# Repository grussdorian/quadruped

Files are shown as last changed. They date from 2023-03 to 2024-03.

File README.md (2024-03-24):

# Final presentation video
[Part 1](https://youtu.be/GLVumrYQS3o)
[Part 2](https://youtu.be/F0bNzEO_wMU)

# Final Paper link

[A Framework for Seamless Trajectory Estimation and Navigation of Robotic Sensor Platform with Resource-Constrained Embedded Controller](https://ieeexplore.ieee.org/abstract/document/10324982)

# Documentation for Pupper

1. [Parts sourcing](#1-parts-sourcing)
2. [Assembly](#2-assembly)
3. [Connections](#3-connections)
4. [Code](#4-code)
5. [Calibration](#5-calibration)
6. [Running the robot](#6-running-the-robot)
7. [Controlling](#7-controlling)
8. [Things which are still left](#8-things-to-do)
9. [Checklist of things before connecting the PCB to the RPi](#9-checklist-of-things-which-are-needed-before-connecting-the-pcb-to-the-raspberry-pi)

## 1. Parts sourcing.

Please refer to [This spreadsheet](https://docs.google.com/spreadsheets/d/1AzzCM8UDrbhDfgtIsiQplI5SMlo7OLG8/edit#gid=1202520655). Part sourcing is listed here comprehensively.

For building the quadruped's body and legs, we have used 5mm fibre sheets. Ideally it should be carbon fibre. But we could not find a vendor who could cut the carbon fibre sheets according to our specifications. Also laser cutting of carbon fibre is not possible in the lab. The next best choice was to use acrylic fibre and that is what we used. $3$ mm thickness for legs and $5$ mm thickness for the base and top.

All the structural elements are taken from [here](https://a360.co/2TEh4gQ)
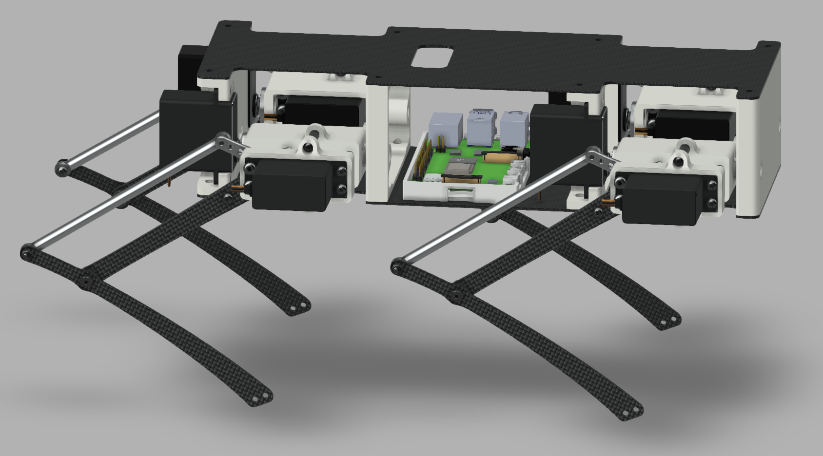
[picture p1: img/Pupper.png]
Pupper Codey the Codecademy mascot (https://stanford195.autodesk360.com/g/shares/SH919a0QTf3c32634dcfedf61e031f673710)


### Laser Cut parts

| Part name | Quantity | Thickness (mm) |
| --- | --- | --- |
| Acrylic fibre plate top | 1 | 5 |
| Acrylic fibre plate bottm | 1 | 5 |
| Lower leg | 4 | 3 |
| Upper leg | 4 | 3 |

To obtain the design of the above parts, we extracted each of the above mentioned prefab from the fusion 360 model. For laser cutting, we had to project the legs, and the base on a 2d surface in fusion, and extract the traces. Then we used laser cad for some final retouching.

_Note:_ The design provided here has two holes in the upper legs, both of them are useless as they do not fit our servo horn. So we had to modify the position of the hole in laser CAD to be $0.85$ mm from the beginning of the curvature. **[Update]** We have used mild steel to make the legs, as the acrylic legs could not handle the heavy weight of the robot

**[Update]** The design of the upper leg has been modified and now we are not using the plastic disc to prevent slipping. Instead we have prototyped (with acrylic) a leg with two holes which fit perfectly in the two holes of the leg. [We are going to laser cut it in aluminum.](#8-things-to-do)

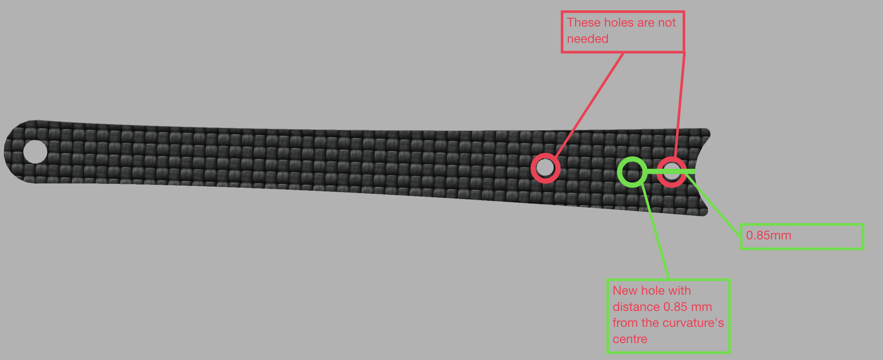
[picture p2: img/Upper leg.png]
Upper Leg


**[Update]** The design of the upper leg has once again been modified. This time there is no disc attached to the upper leg. Instead the concave shape of the upper leg has been changed to a convex shape, with two M3 screw holes. Thus the need for adding a disc has been eliminated.

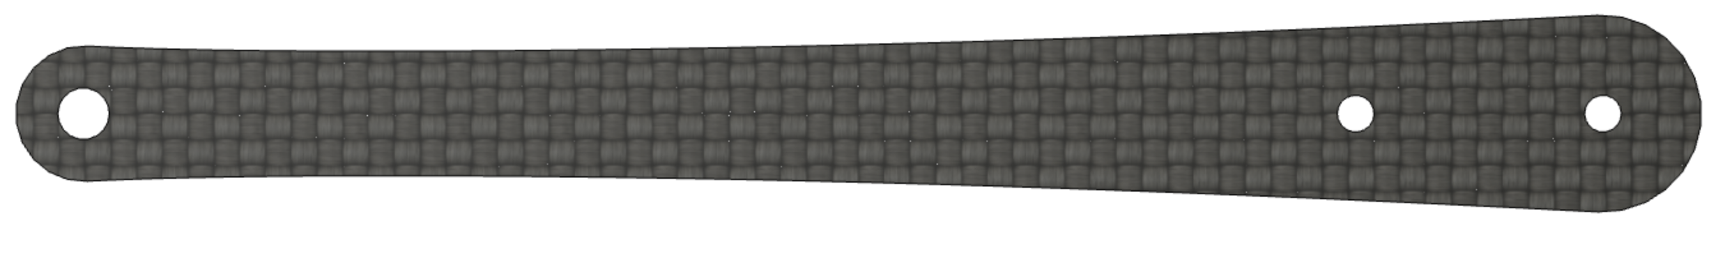
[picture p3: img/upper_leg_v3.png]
Upper Leg


### 3D printed parts

_Note that the 3D printed parts had holes much bigger than the size of the inserts. So the inserts did not fit in the holes. Instead we tried to use nuts and washers to tighten the screws where the inserts would have gone_

For the 3D printed Structures, we used PLA or PETG, 0.2mm-0.4mm layer height, >50% infill.

| Part name | STL name | Quantity |
| --- | --- | --- |
| Body support - "Front1" | FrontFront.stl | 1 |
| Body support - "Front2" | FrontBack.stl | 1 |
| Body support - "Back1"  | BackFront.stl | 1 |
| Body support - "Back2"  | BackBack.stl | 1 |
| Inner Hip | HipInsideFDM.stl  | 4 |
| Outer Hip | HipOutsideFDM.stl | 4 |

All the parts are uploaded in the [3D printed files](/3DPrintedFiles/)

After all the raw materials and parts are available, we can move to assembly

### PCB

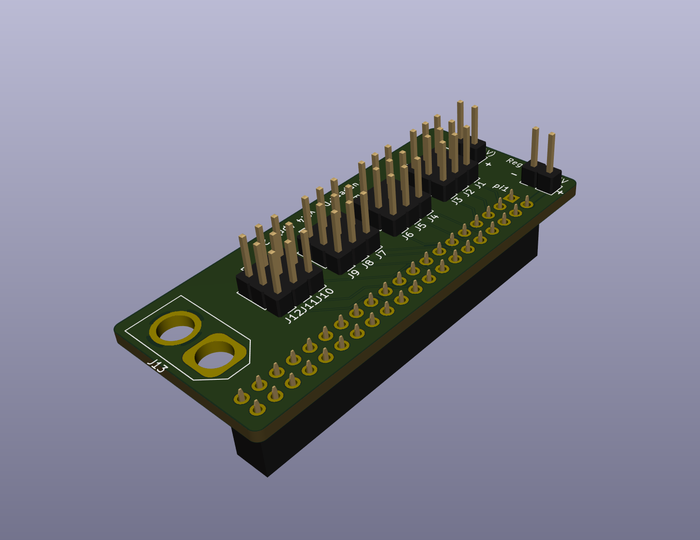
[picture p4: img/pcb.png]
PCB
 required to power all the servos, provide signal from the Raspberry Pi. It sits on top of the GPIO pins of the Pi. It can also be used to power the Pi [something we messed up doing](#what-went-wrong).
The [Gerber files](https://github.com/stanfordroboticsclub/Pupper-Raspi-PDB/) could be used to print the PCB using any standard PCB manufacturer. _NOTE_ 2 oz copper should be used for the traces. After getting the PCB, we need to solder the headers as shown in the image. Solder a pigtail connector wire in J13 to connect the battery. Make sure that the pigtail wire is joined above (side facing the male headers) the PCB. Solder the female $20\times2$ female header on the back side of the PCB.

**[Update]** There was jittering, (i.e incorrect pwm signals) in for J3. So we had to cut out the header for the signal pin of J3 and attach a jumper wire from GPIO pin `20` to signal socket of J3 directly. In future PCBs This change is to be [incorporated](#8-things-to-do)

## 2. Assembly

Pupper has 4 legs, each with 3 sets of [servos](https://robokits.co.in/motors/rc-servo-motor/ultra-torque-metal-gear-35kgcm-coreless-stainless-steel-pinion-standard-servo-motor). These servos are placed inside 3D printed hip joints.

### All reference images are placed under folder [img](/img)

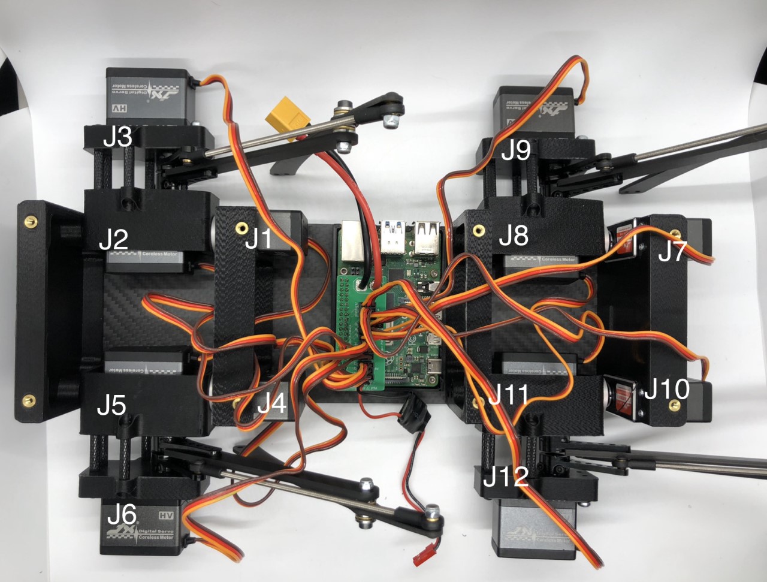
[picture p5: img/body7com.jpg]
Servo placement and numbering


### Hip assembly

All the servos should be housed inside hip joints in the following way:

1. First, screw metallic disc with $J1,J4,J7,J10$. _Important_: apply some hot glue after fixing the disc tightly with the servo.

2. Take inner hip and screw 4 black m4x6 screws that came with the servos to the disc.

3. Place $J2,J5,J8,J11$ in the inner hip and use m3x20 screws to tighten the side of the hip facing away from the disc.

4. _Note:_ Tightening should be enough such that the screw pokes out from the other side of the inner hip. Here we need to fasten the 20mm spacers. Tighten the servo with m3x10 screws (for the remaining two holes)

_Choice of the screw is important. The horn should be facing away from the 4 spacers and should be able to rotate freely without any obstruction. So the screws should be tightened upto that extent only which does not cause any obstruction in the horn's way_

5. Place the other set of 20mm spacers on the screws fastened on the sideof the plastic case, i.e they do not tighten the servo.

   Then the plastic disc that came with the servos should be attached ring side facing up, to $J5,J2,J8,J11$ along with 25T servo horn beneath the disc (which came with the servos as well).

_The disc is used to create spacing for the legs. It makes sure that the legs don't slip while rotating._

6. Attach 25T horn to $J3,J6,J9,J12$. This horn should parallel to the other set of horns i.e $J5,J2,J8,J11$ and should face the free side of the enclosure.

### Leg assembly

Take the laser cut parts, upper legs and lower legs and place a thrust bearing between the two joints, and another bearing to the side of the screw head. The flat end of the lower leg should touch the ground and the lower leg should be facing outwards, away from the body. Place a m3x16 screw between the sandwitched joints and tighten a nylon locknut from the other end. This way prepare all the 4 legs.

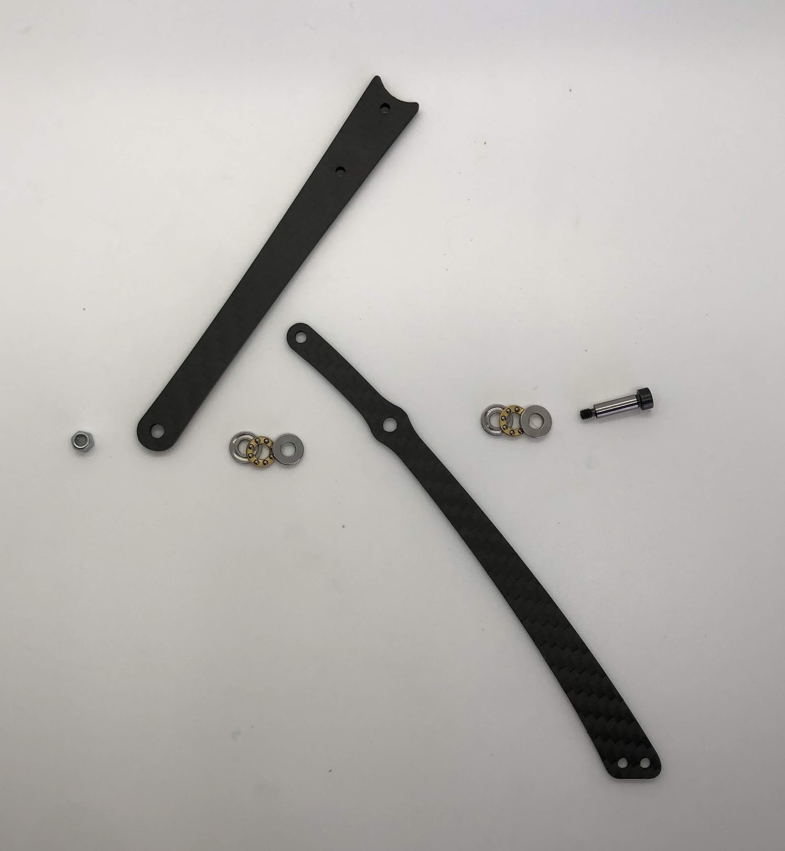
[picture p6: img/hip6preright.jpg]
hip6


Connect the upper legs to $J5,J2,J8,J11$, with a m3x10 screw. The curvature of the upper leg should fit just right in the disc. The disc is there to prevent the le from slipping.

### Muscles

After legs have been attached to the servos, take two ball joints and tighten a threaded piece of metal between two ball joints. The length from one hole to another hole should be exactly $123.5$ mm, for all 4 sets of muscles.

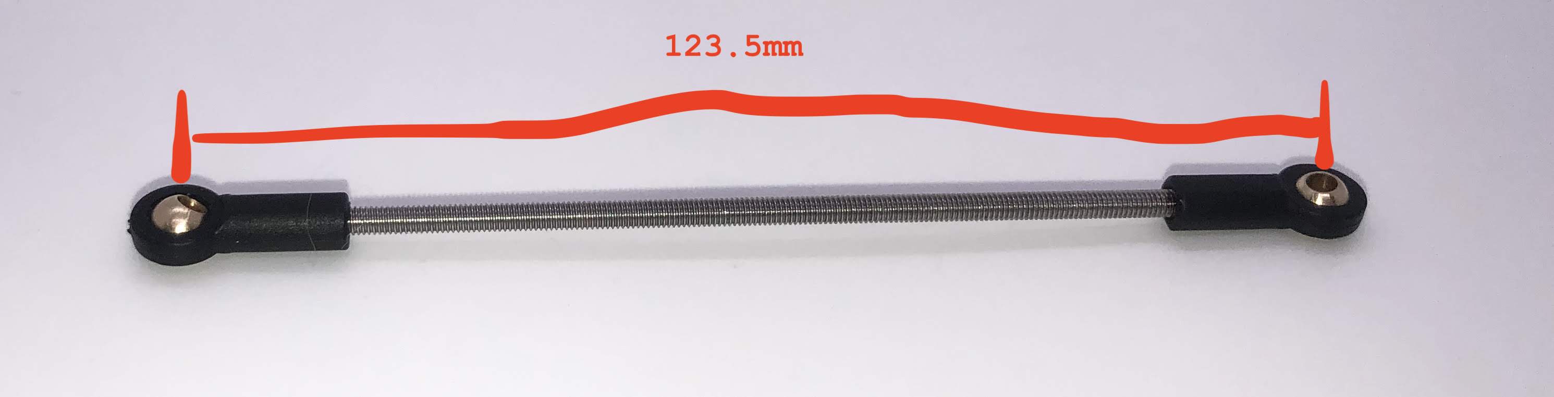
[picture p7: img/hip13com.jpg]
hip13


Connect the four muscles with a m3x8 screw to the horns of the servos $J3,J6,J9,J12$. Connect the other end to the hole made in the extreme upper part of the lower leg.

All 4 legs are ready now.

### Body assembly

Take the laser cut base of the body and put all the 3D printed structure on the corresponding place. Take m3x16 screws and a washer. Put the washer on the plastic and screw to the other end. Fasten the screw with a normal locknut.

Place all the plastic parts and tighten them to the base of the body. Now place $J1,J4,J7,J10$ in their respective positions and tighten them with screws. All the legs are now attached to the body.

Now we can proceed to wiring and after than we would need to attach the upper part of the body.

## 3. Connections

$$
  yellow \rightarrow signal
$$

$$
  red \rightarrow power
$$

$$
  brown \rightarrow ground
$$

All the servos should be connected to the [PCB](https://github.com/stanfordroboticsclub/Pupper-Raspi-PDB/), which is connected to the Raspberry Pi. The PCB is well marked and the signal side of the connector should face the GPIO headers.

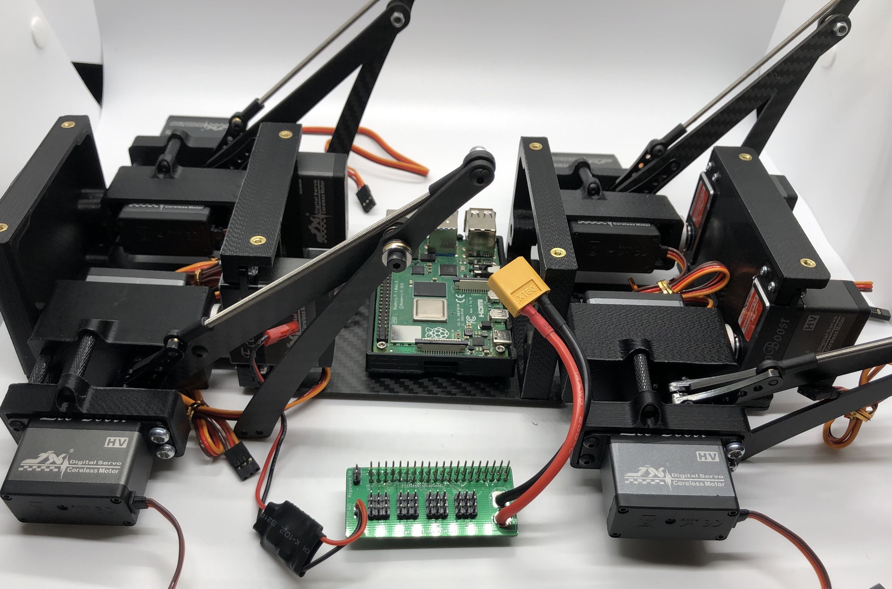
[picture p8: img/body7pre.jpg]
Connection

The pigtail connector (Big wire on the right) is connected to the battery powering 7.4 volts and that power is converted to 5 volts using a voltage converter on the left. The output of the voltage converter _should_ be 5 Volts which directly plugs in our PCB where it is marked +5 volts and ground.

## What went wrong

Never try to power the RPi with anything less than 4.75 volts and 5.25 volts. This was the mistake which costed us our Raspberry Pi 3 model B plus.
I tested the output of the voltage converter, which showed 5 volts and I powered on the Raspberry Pi. It turned on and I SSHed into the Pi. Tested one servo and it was all good. Then I turned off the RPi using shutdown command from SSH.

However next time before turning on the RPi I did not check the voltage and it didn't turn on. I quickly unplugged the battery and then disconnected the board. Later when I was testing the voltage converter separately, the output of the voltage converter was same as the input with some voltage drop i.e it was showing 6.8 volts!

Assuming our worst fear, I waited for another day and checked online forums whether the RPi has polyfuse or not. It turns out that the Raspberry Pi has polyfuse, but they are placed between the input and the SOC so the GPIO side where we plugged in our power supply had no protection.

I double checked all the [testing points](https://ozzmaker.com/testing-points-raspberry-pi/) in the Pi and confirmed that the raspberry pi has indeed been shorted.

**NOTE** Always check the power supply before plugging into the Pi. Since it is powered by micro USB we might be tempted to power it on from our computer's USB port but **DON'T** do that as that port can never provide enough current to the board. Similarly always check for faulty power supply and voltage levels before powering on the Pi.

## 4. Code

Code for the quadruped has been taken from the open source project by Stanford robotics group [here](https://github.com/stanfordroboticsclub/StanfordQuadruped) and the joystick controller code has been taken from [here](https://github.com/stanfordroboticsclub/PS4Joystick). The code is very well documented and self explanatory but it had an [issue](#added-wireddongle-controller-support)

I did not use the image they provided for flashing the SD card. The image is way to old and I faced many problems while updating repositories. Thus I ended up using a standard 32 bit distribution of [Raspbian](https://www.raspberrypi.com/software/operating-systems/#raspberry-pi-os-32-bit).

After etching the SD card with [Raspberry Pi's image software](https://www.raspberrypi.com/software/) I booted into the Pi.

Raspbian provides a GUI so our job was easier. Later the plan was to remove the Desktop Environment and only keep the CLI to reduce system overhead.
With the pi connected to USB mouse, keyboard and a display, we set up wifi on the pi so we could use it in headless mode in the future. All successive accesses were made using VNC or SSH. And the pi was only connected to power using a wall adapter which supported 3A 5V.

**[Update]** Fixed a bug with the controller, forward and backward movements are now correctly oriented.

### Added wired/dongle controller support

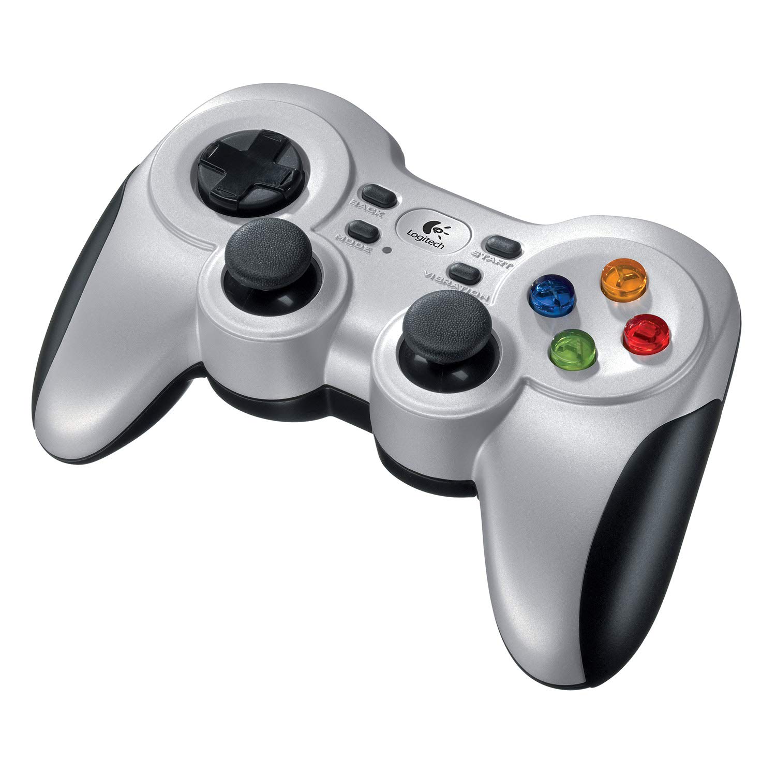
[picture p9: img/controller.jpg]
controller
The default code They provided had only support for a PS4 Dualshock controller. And not only that, the internal code for the working of the robot, is also very much intertwined with the proprietary code it shipped with. Thus I had to rewrite the code to add support for wired / standard bluetooth controller with a dongle like the Logitech f710 controller we used. 

The modified code is [here](https://github.com/grussdorian/PupperCommand) and [here](https://github.com/grussdorian/pupper)

### What were the changes?

Dualshock 4 uses a proprietary protocol to communicate to the bluetooth connected device. The Python package to parse the input stream is also hacky and reverse engineered. Dualshock 4 is also very expensive. So adding support for generic X-input supported controllers were a requirement.

The data buffer sent received by the Python package is a dictionary

```python
input_buff = {
"LS":0.6501,
"RS":-0.1304,
"x":1,
"triangle":0,
"square":1,
"circle":1,
"L1": 1
"L2": 0.2452
....
}
```

The values may not be normalised but float values $\in [-128,127]$. So they were normalised between -1 to 1.
Then the UDP connection objects that were communicating with the controller were deleted.

The connection to the controller part has been completely re-written. It still uses UDP but the events fired by the UDP publisher object is interrupt driven (from the usb). Thus, this is more efficient in terms of polling in regular intervals (which dualshock 4 was doing). The only caveat is now the publisher has to publish in two different ports, one for activating the robot and another for driving the robot, while the first one listens for shutdown command.
This is a quick way of doing things but I will soon change the code to only publish to one port.

## 5. Calibration

To calibrate the servos, first we need to set the servo to its neutral position without the horns, then test whether they can move freely (whether addition of the horns would create an obstruction in the path of the servo).

To do this, first we need to plug in the servo individually to the PCB and power on the Raspberry Pi. If `robot.service` is running, first stop it by `sudo systemctl stop robot.service`. Then cd to the directory `servo_code/quadruped/servo_code/` and modify the file `move_to_zero.py` with the servo which we are currently trying to move.

`move_to_zero.py` Takes two command line arguments:-

1. min
2. max

i.e

```console
pupper@pupper cd servo_code/quadruped/servo_code/
pupper@pupper/servo_code/quadruped/servo_code/ python3 move_to_zero.py min
```

would move the servo which is currently being selected in the code.

Change the part of the code as:

```python
servo_JXX = Servo(JXX, min_pulse_width=MIN_PULSE_WIDTH,
                 max_pulse_width=MAX_PULSE_WIDTH, pin_factory=factory)
```

Change X with the number of servo you want to move to min or max

i.e

```python
servo_J10 = Servo(J10, min_pulse_width=MIN_PULSE_WIDTH,
                 max_pulse_width=MAX_PULSE_WIDTH, pin_factory=factory)
```

Then run the code:

```console
pupper@pupper/servo_code/quadruped/servo_code/ python3 move_to_zero.py min
```

To move the servo to its min position. Accordingly place the hip joints **only after making sure that there is no obstruction**

**Note if the horn gets stuck, it can potentially damage the servo and widen the dead-zone for the servo. (Which means without putting any load on the servo, it would wobble every so slightly. This wobble might increase when the horn is stuck and the servo is trying its best to push it against the metal standoffs, acrylic body or the plastic frame)**

The correct alignment of the horns is as follows:

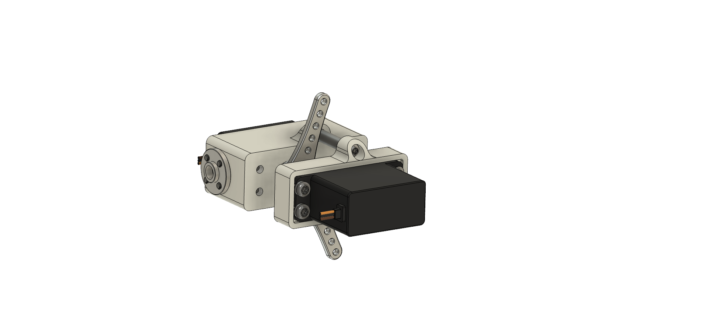
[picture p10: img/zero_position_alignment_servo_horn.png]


Note that the horns are just barely touching the metal standoffs. For the inner hip (servo behind) the horn is at its max. The servo in the front is at its min. This position is chosen such that when the leg tries to adjust every time when the following calibration code is run, or when the robot is [activated using the controller](#6-running-the-robot), the default position is such that nothing gets obstructed.

Earlier the horns were vertical, which was creating obstruction when the robot was [being activated](#6-running-the-robot). It had to be taken to the walking position as soon as possible.

### To run the calibration code

First, stop the `robot.service` and start `calibrate_servos.py`.
The pulse width for our servos is as follows:

By following the [datasheet](https://github.com/microrobotics/DS3235-270/blob/master/DS3235-270_datasheet.pdf) of our servo, which says

`max_pulse_width = 2500` $\mu$ seconds

`min_pulse_width = 500` $\mu$ seconds

Thus entire range of pulse width lies $\in$ [2500,500]
So the width of the pulse is $2500-500=2000 \mu$ seconds

And the maximum allowed rotation electrically is $180\degree$

Thus pulse width for rotating $1\degree$ is

$$
\frac{2500-500\mu sec}{180\degree} = 11.111 \mu sec
$$

By default the values provided was $11.333 \mu sec$ which we have to override in `calibrate_servos.py`

Final calibration matrix is as follows. Note these values are not the final values and are subject to change as we continue to improve the design.

| Servo name | Offset Angle | Final angle |
| --- | --- | --- |
| J1 | 2 | -2 |
| J2 | -52 | 97 |
| J3 | 32 | -77 |
| J4 | 1 | -1 |
| J5 | -50 | 95 |
| J6 | 29 | -74 |
| J7 | 2 | -2 |
| J8 | -39 | 84 |
| J9 | 34 | -79 |
| J10 | 4 | -4 |
| J11 | -49 | 94 |
| J12 | 27 | -72 |

## 6. Running the robot

Before starting the robot, we need to make sure that the service `joystick.service` is running. This service is an instance of the python code `Joystick.py` in the folder `Pupper Command`. The code is used to interface the joystick with the robot. To check whether it is already running

```console
pupper@pupper sudo systemctl status joystick.service
```

If the service is not running, run it using the command

```console
pupper@pupper sudo systemctl start joystick.service
```

To run the robot using the controller

```console
pupper@pupper sudo pigpiod
pupper@pupper cd StanfordQuadruped/
pupper@pupper/StanfordQuadruped/ python3 run_robot.py
```

The file `run_robot.py` is the entry point for starting the robot.
By default, there is a service `robot.service` located in the root of the project folder which directs the shell environment to run the python command run_robot.py using python3.

### Jittering and GPIO daemon

The service also directs the shell environment to activate Raspberry Pi's GPIO pins prior to activating the robot by running the command `sudo pigpiod` to activate the Pi's GPIO daemon service. Without this command being issued in the first place `run_robot.py` can not run. Thus when we are manually starting the robot we need to make sure that the GPIO daemon is running and the command is activated exactly once.

If the command `sudo pigpiod` is issued more than once, the shell will prompt an error that a shared resource is being used by multiple processes. This will cause cause a race condition and wrong pwm signals will be delivered to the GPIO pins. **Thus to stop the jittering** we need to restart the Raspberry Pi.

**NOTE:** The service `robot.service` runs the command `sudo pigpiod` once before the service starts. Thus if the service is running, there is nothing else we have to do. Just press `L1 (or LB)` on the controller to activate the robot. The logs of the program will be visible in the service logs by `sudo systemctl status robot.service`.

**But** if we want to run the robot manually, first we need to stop `robot.service`

First check whether the service is already running

```console
pupper@pupper/StanfordQuadruped/ sudo systemctl status robot.service
```

Stop the service if it is already running

```console
pupper@pupper/StanfordQuadruped/ sudo systemctl stop robot.service
```

Then run the code

```console
pupper@pupper/StanfordQuadruped/ python3 run_robot.py
```

## 7. Controlling

After the robot is activated using `L1 (or LB)` one can run the robot.
Make sure the controller is in X-input mode and the mode button on the controller is not lit up.
You can debug the commands from the controller on the screen, `run_robot.py` logs all the commands that are being sent from the controller.
If the light on the mode button is on, that means the analog sticks are emulating the d-pad buttons. Thus only discrete value of `1` and `-1` are obtained by the program.

### Pupper can transition to 3 modes.

1. Standing
2. Squatting
3. Normal

Cycle among each of these modes by pressing the `A (green)` button on the controller. When the robot is in normal mode, press `R1 (or RB)` to activate walking mode. This would allow the controller to control pupper using the analog sticks. Left analog stick can be used to move it forwards or backwards.
Press `R1 (or RB)` once more to reset to normal mode. Here one can set the heights of the joints and legs by pressing `X`, `B` or `Y` buttons on the controller. Pupper can also sit by lowering its lower legs and straightening its front legs.

## 8. Checklist of things we did

1. Mount the battery to the bottom of the robot and fasten it with electrical tape and zip-ties.
2. Test the buck converter whether proper 5 volts are coming on the output pins or not.
3. Make an over-voltage protection circuit with Zener diode.
4. We have to recalibrate the robot after the aluminum legs arrive.
5. We have to change the PCB design so the signal for J3 comes from GPIO pin `20`.
6. We need to replace the screws in the legs with longer screws.
7. Think about adding a support to the cantilever structure of the inner servos.

## 9. Checklist of things which are needed before connecting the PCB to the raspberry pi.

1.  Check all the pins from raspberry's GPIO by hooking them up with an oscilloscope and verifying whether the signals are correct or not. Use a female header to stab the PI's GPIO pin and take the male end of that wire and hook them to the oscilloscope. (Also take a ground pin out from the Pi for hooking the ground lead from the probe) For instance, for our servos, the period of the signal is $20$ _ms_ and lowest admitted duty cycle is $\frac{4}{20}$ _ms_. This should be verified for the entire range of permissible duty cycles for the servo's min and max positions.
    In our case, we did not get a proper signal for GPIO pin `4` for servo J3, thus we changed the pin number to GPIO `20` and added a jumper wire from the same pin to J3's signal header.

2.  Take the multimeter to short circuit testing mode, (a buzzer will make sound when the two leads of the meter are shorted).
    Then probe

        a. Each ground pin with every other pin and check whether those points which should be ground are shorted.

        b. Each power pin with every other pin and check that no pin other than the pins meant to supply power are shorted or not

        c. Each signal pin (where the servos plug in) and the Pi's header pins and test whether the signal pins are properly connected and whether any other pin is shorted with the signal pins.

        d. Most importantly, check whether Vcc and Gnd are not shorted!

This will make sure that all connections are proper and there is no harm to the components after connecting the PCB to the Raspberry Pi and powering it on.

Power the raspberry Pi from the power bank. Later a buck converter and a protection circuit will also be used.

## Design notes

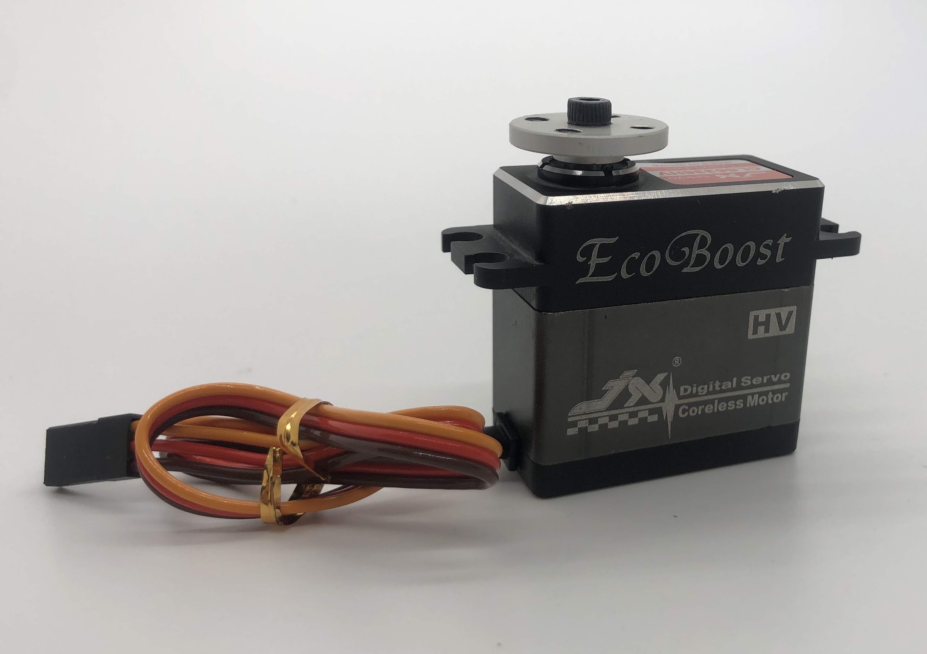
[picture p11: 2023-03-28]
img/hip1com.jpg

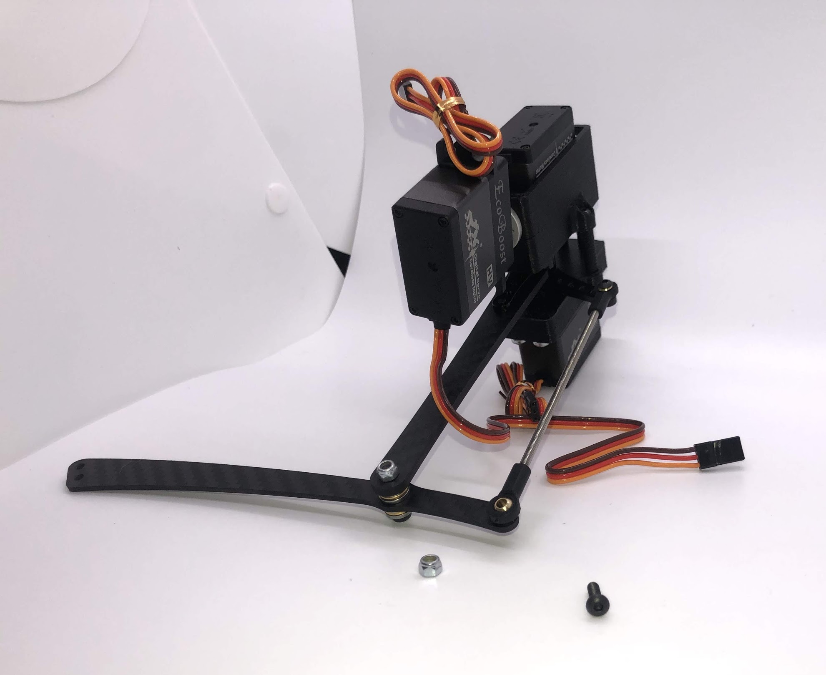
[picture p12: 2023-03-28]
img/hip15pre.jpg

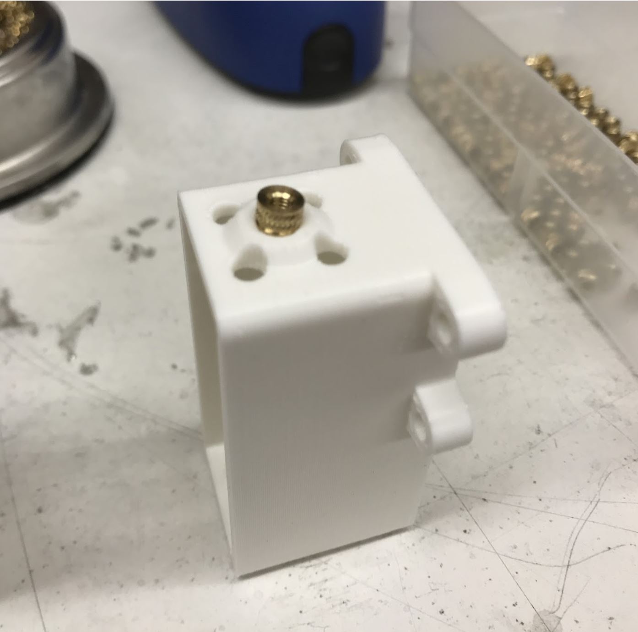
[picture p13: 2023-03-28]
img/hip2pre.jpg

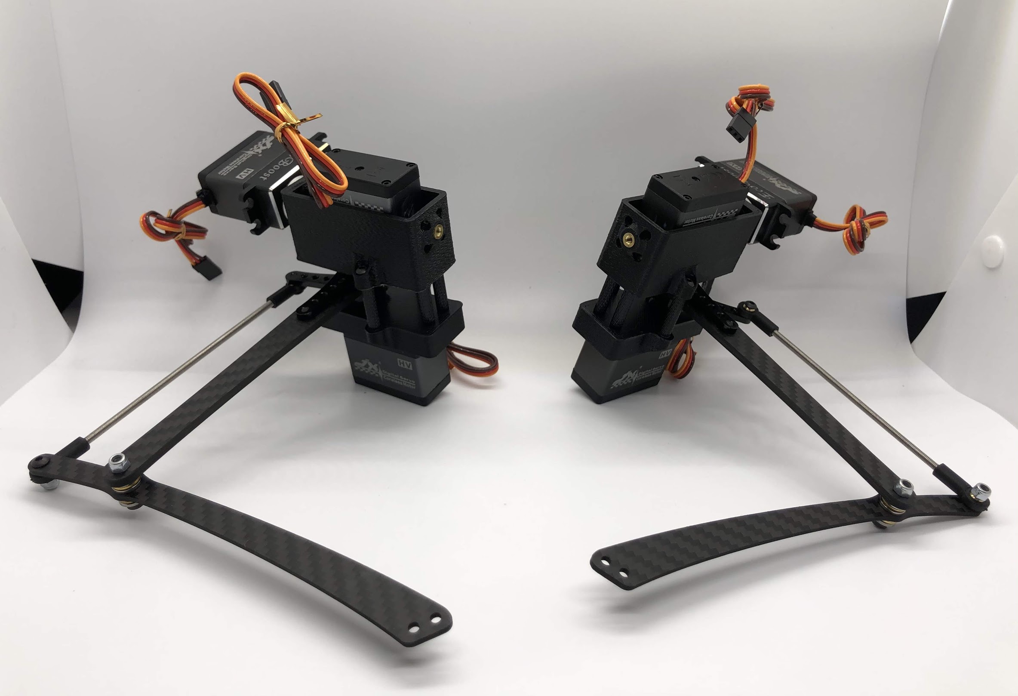
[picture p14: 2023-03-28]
img/hip16an.jpg

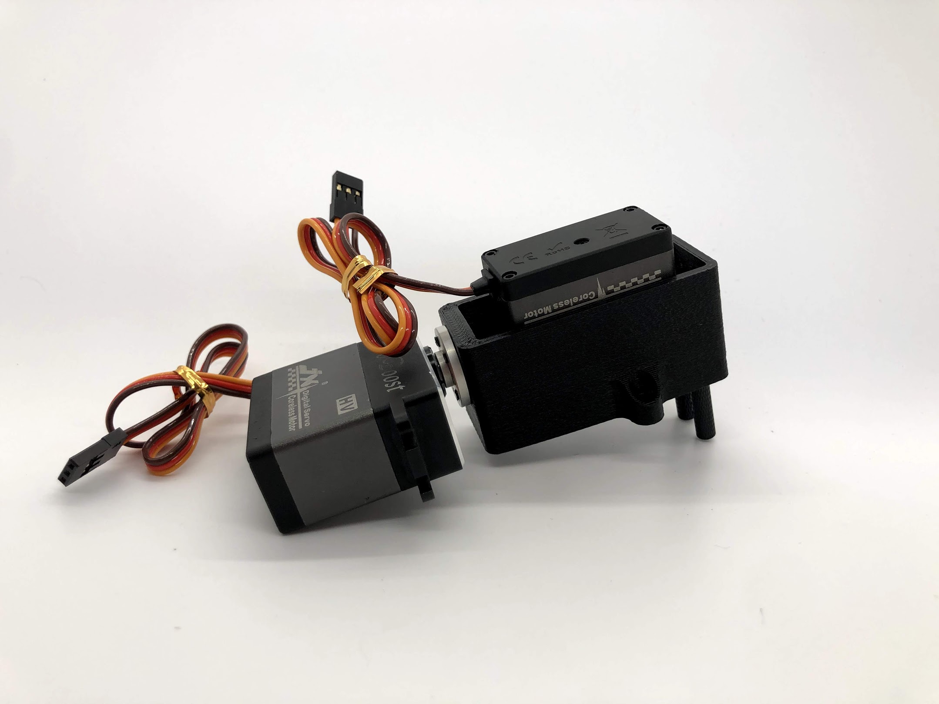
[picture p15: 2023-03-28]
img/hip4com.jpg

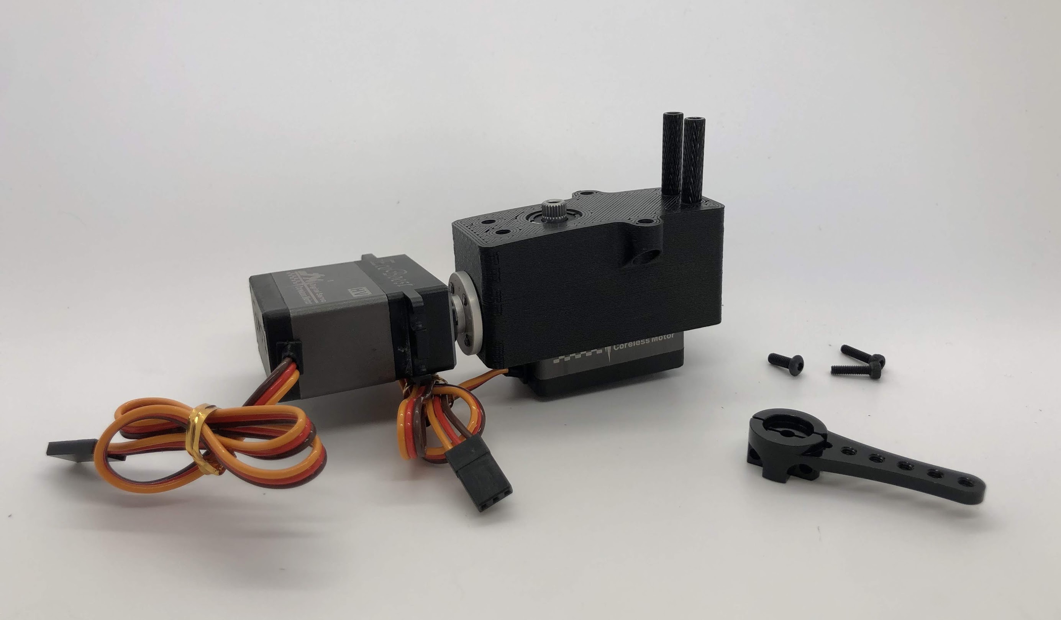
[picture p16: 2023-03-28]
img/hip5pre.jpg

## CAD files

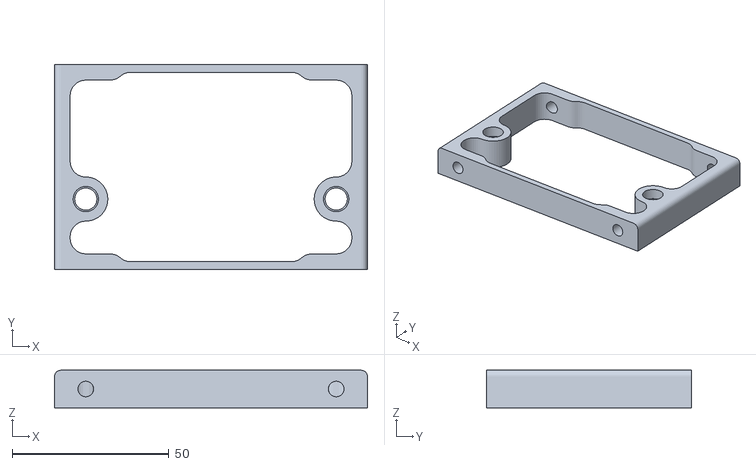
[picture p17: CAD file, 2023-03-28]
3DPrintedFiles/BackFront.stl
100.0 x 65.5 x 12.0

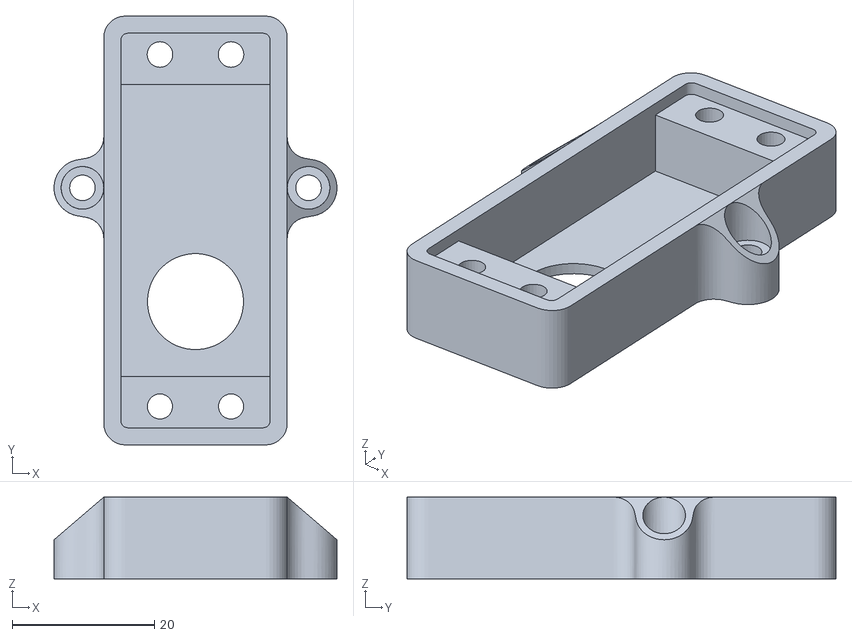
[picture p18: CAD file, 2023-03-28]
3DPrintedFiles/HipOutsideFDM.stl
39.8 x 60.3 x 11.5

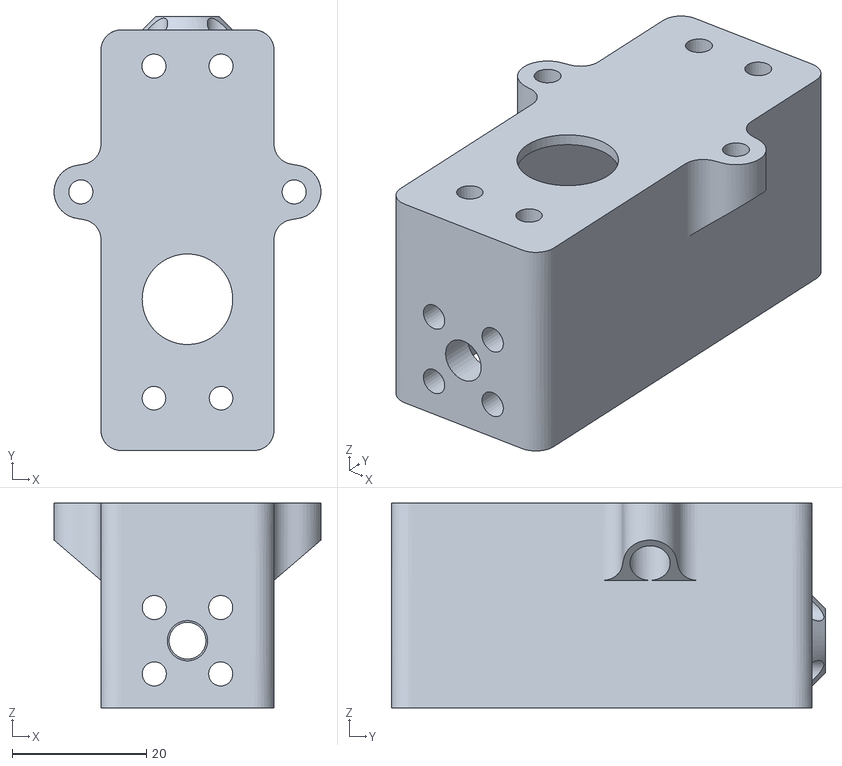
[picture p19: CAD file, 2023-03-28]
3DPrintedFiles/HipInsideFDM.stl
39.8 x 64.7 x 30.5

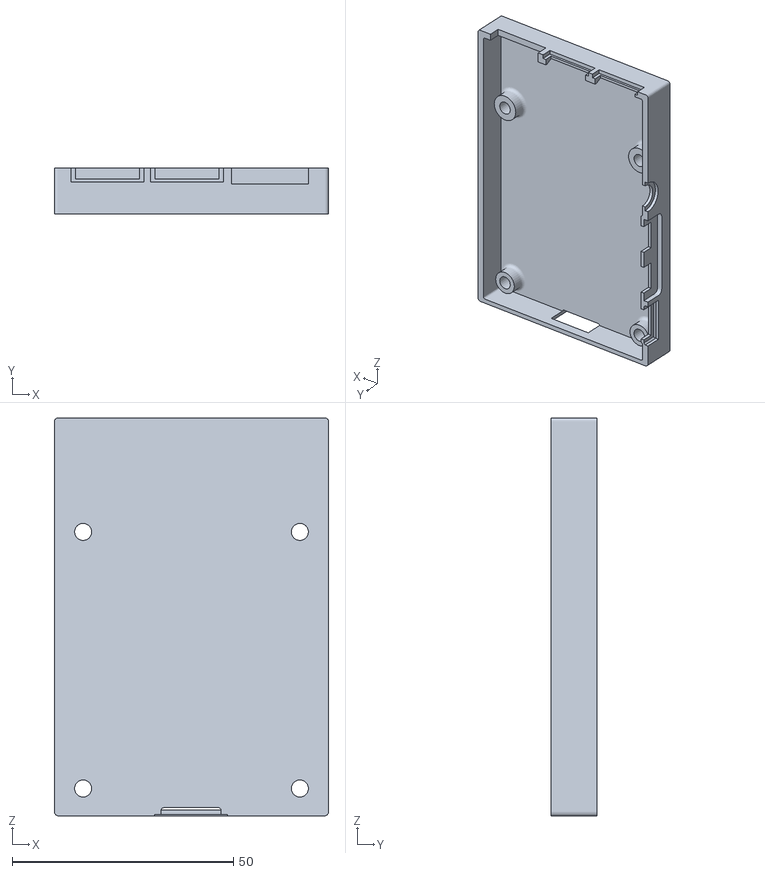
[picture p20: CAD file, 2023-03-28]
3DPrintedFiles/picase.stl
62.0 x 10.3 x 90.0

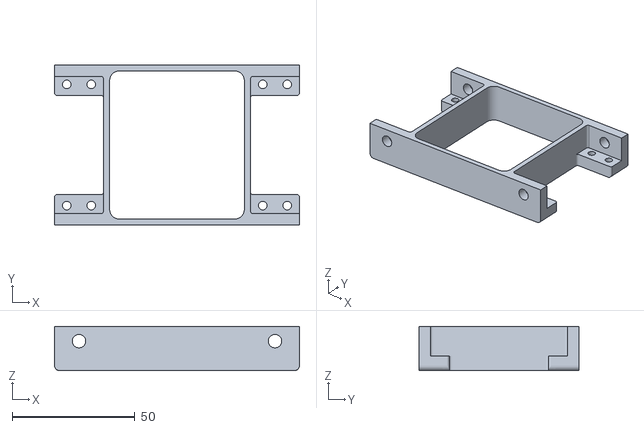
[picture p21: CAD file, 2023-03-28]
3DPrintedFiles/FrontBack.stl
100.0 x 65.5 x 18.0

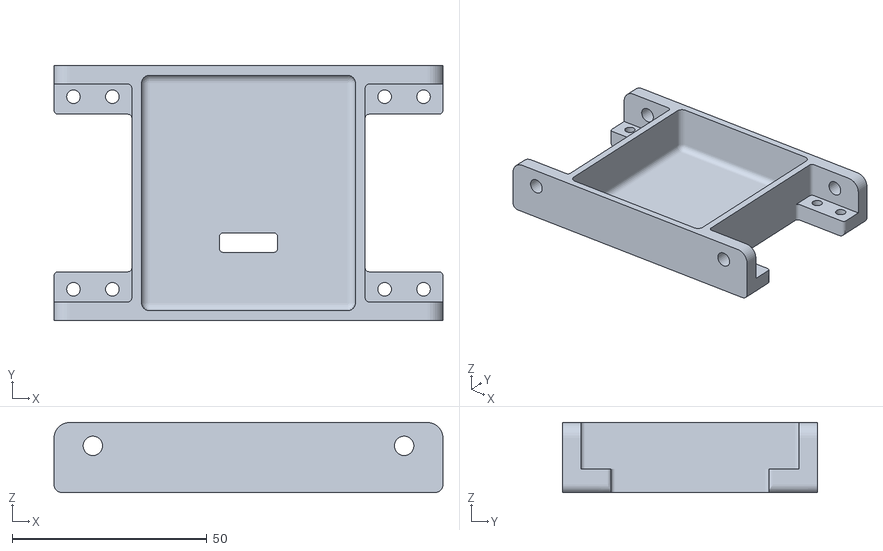
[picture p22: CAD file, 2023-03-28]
3DPrintedFiles/BackBack.stl
100.0 x 65.5 x 18.0

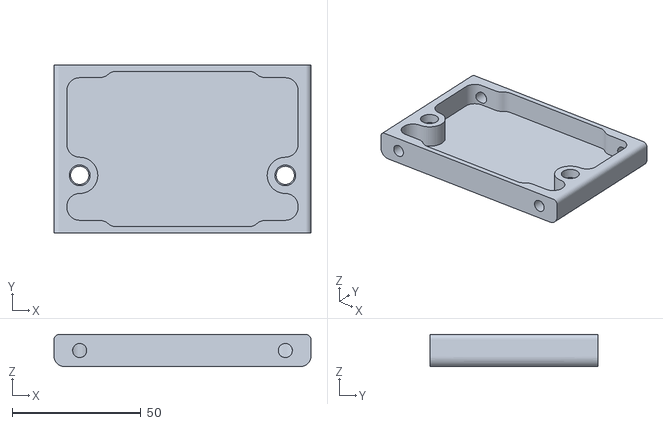
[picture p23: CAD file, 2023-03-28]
3DPrintedFiles/FrontFront.stl
100.0 x 65.5 x 12.5

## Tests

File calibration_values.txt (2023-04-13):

J1  2   -2
J2 -52  97
J3  32 -77

J4  1   -1
J5 -50  95
J6  29 -74

J7  2   -2
J8 -39  84
J9  34 -79

J10 4   -4
J11 -49 94
J12  27 -72

 CALIBRATION COMPLETE!

Calibrated neutral angles:
[[ -2.  -1.  -2.  -4.]
 [ 97.  95.  84.  94.]
 [-77. -74. -79. -72.]]

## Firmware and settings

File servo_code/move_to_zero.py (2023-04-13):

from gpiozero import Servo
from time import sleep
import sys
from gpiozero.pins.pigpio import PiGPIOFactory

factory = PiGPIOFactory()

J1 = 2
J2 = 3
J3 = 20
J4 = 14
J5 = 15
J6 = 17
J7 = 18
J8 = 27
J9 = 22
J10 = 23
J11 = 24
J12 = 25

MIN_PULSE_WIDTH = 500/1000000
MAX_PULSE_WIDTH = 2500/1000000

servo = Servo(J1, min_pulse_width=MIN_PULSE_WIDTH,
                 max_pulse_width=MAX_PULSE_WIDTH, pin_factory=factory)
# servo2 = Servo(J5, min_pulse_width=MIN_PULSE_WIDTH,
#                  max_pulse_width=MAX_PULSE_WIDTH, pin_factory=factory)
mode = sys.argv[1]
if mode == "min":
    # MIN
    servo.min()
    # servo2.max()
    sleep(0.5)
    
if mode == "max":
    # MIN
    servo.max()
    # servo2.min()
    sleep(0.5)

if mode == "mid":
    # MID
    servo.mid()
    # servo2.mid()
    sleep(0.5)

print("Clean exit")
factory.close()  # Prevents the servos from jumping to the previously written state immediately after powering on

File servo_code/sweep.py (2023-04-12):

from gpiozero import Servo
import math
from time import sleep

from gpiozero.pins.pigpio import PiGPIOFactory

factory = PiGPIOFactory()

J1 = 2
J2 = 3
J3 = 20
J4 = 14
J5 = 15
J6 = 17
J7 = 18
J8 = 27
J9 = 22
J10 = 23
J11 = 24
J12 = 25

# Neutral positions for the following servos
# J1_NEUTRAL = math.radians(-24)
# J4_NEUTRAL = math.radians(-26)
# J7_NEUTRAL = math.radians(-28)
# J10_NEUTRAL = math.radians(-33)

# J2_NEUTRAL = 0
# J5_NEUTRAL = 0
# J8_NEUTRAL = 0
# J11_NEUTRAL = 0


MAX_INNER_SERVO = 0
MIN_INNER_SERVO = -50

MAX_OUTER_SERVO = 360
MIN_OUTER_SERVO = 0

MIN_PULSE_WIDTH = 500/1000000
MAX_PULSE_WIDTH = 2500/1000000

# servo_J1 = Servo(J1, min_pulse_width=MIN_PULSE_WIDTH, max_pulse_width=MAX_PULSE_WIDTH, pin_factory=factory)
# servo_J2 = Servo(J2, min_pulse_width=MIN_PULSE_WIDTH, max_pulse_width=MAX_PULSE_WIDTH, pin_factory=factory)
# servo_J3 = Servo(J3, min_pulse_width=MIN_PULSE_WIDTH, max_pulse_width=MAX_PULSE_WIDTH, pin_factory=factory)

# servo_J4 = Servo(J4, min_pulse_width=MIN_PULSE_WIDTH, max_pulse_width=MAX_PULSE_WIDTH, pin_factory=factory)
servo_J5 = Servo(J5, min_pulse_width=MIN_PULSE_WIDTH,
                 max_pulse_width=MAX_PULSE_WIDTH, pin_factory=factory)
servo_J6 = Servo(J6, min_pulse_width=MIN_PULSE_WIDTH,
                 max_pulse_width=MAX_PULSE_WIDTH, pin_factory=factory)

# servo_J7 = Servo(J7, min_pulse_width=MIN_PULSE_WIDTH, max_pulse_width=MAX_PULSE_WIDTH, pin_factory=factory)
# servo_J8 = Servo(J8, min_pulse_width=MIN_PULSE_WIDTH, max_pulse_width=MAX_PULSE_WIDTH, pin_factory=factory)
# servo_J9 = Servo(J9, min_pulse_width=MIN_PULSE_WIDTH, max_pulse_width=MAX_PULSE_WIDTH, pin_factory=factory)

# servo_J10 = Servo(J10, min_pulse_width=MIN_PULSE_WIDTH, max_pulse_width=MAX_PULSE_WIDTH, pin_factory=factory)
# servo_J11 = Servo(J11, min_pulse_width=MIN_PULSE_WIDTH, max_pulse_width=MAX_PULSE_WIDTH, pin_factory=factory)
# servo_J12 = Servo(J12, min_pulse_width=MIN_PULSE_WIDTH, max_pulse_width=MAX_PULSE_WIDTH, pin_factory=factory)

# servo_J1.value = math.sin(J1_NEUTRAL)
# servo_J4.value = math.sin(J4_NEUTRAL)
# servo_J7.value = math.sin(J7_NEUTRAL)
# servo_J10.value = math.sin(J10_NEUTRAL)

try:
    while True:
        for i in range(MAX_INNER_SERVO, MIN_INNER_SERVO-1, -1):
            servo_J5.value = math.sin(math.radians(i))
            servo_J6.value = math.sin(math.radians(i))
            # servo_J9.value = math.sin(math.radians(i))
            # servo_J12.value = math.sin(math.radians(i))

            # servo_J2.value = math.sin(math.radians(i))
            # servo_J5.value = math.sin(math.radians(i))
            # servo_J8.value = math.sin(math.radians(i))
            # servo_J11.value = math.sin(math.radians(i))

            # servo_J1.value = math.sin(math.radians(i))
            # servo_J4.value = math.sin(math.radians(i))
            # servo_J7.value = math.sin(math.radians(i))
            # servo_J10.value = math.sin(math.radians(i))
            sleep(0.01)


except KeyboardInterrupt:
    print("Clean exit")
    factory.close()  # Prevents the servos from jumping to the previously written state immediately after powering on

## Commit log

2023-03-02 servo calibration code added
2023-04-12 fixed MAX_OUTER_SERVO value and added code to calibrate servo to its neutral position. Must be run without the horns attached!
    [move_to_zero.py, sweep.py]
2023-04-13 calibration and move to zero
2023-04-17 Docs, Calibration Value
2023-04-24 datasheet of servo added
2023-04-25 Added calibration values, fixed bug added docs
2023-05-05 changed calibration values
